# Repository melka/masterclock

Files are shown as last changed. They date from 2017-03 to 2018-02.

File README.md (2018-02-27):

# masterclock

Master clock for Lepaute 30 seconds alternating pulse slave clock and possibly other models.

## background

Slave clocks are old school clocks mostly used in train stations, hospitals, factories, etc... places that needed to have accurate timekeeping and synchronized clocks in a lot of places. A master clock was responsible for keeping time and controlling all the slave clocks. There were a number of clock manufacturers, and there were a lot of way of synching the slave clocks to the master clock.

If you find a beautiful industrial slave clock, there are several options :
* Find the master clock to go with it, but you'll need space, money and time to take care of it
* Remove the old mechanical movement and replace it with a quartz one (shame on you)
* Buy one of [these](http://www.bmumford.com/clocks/driver/driver.html), but what's the fun in that ?
* Make a teeny-tiny master clock.

So here comes this project.

## goal

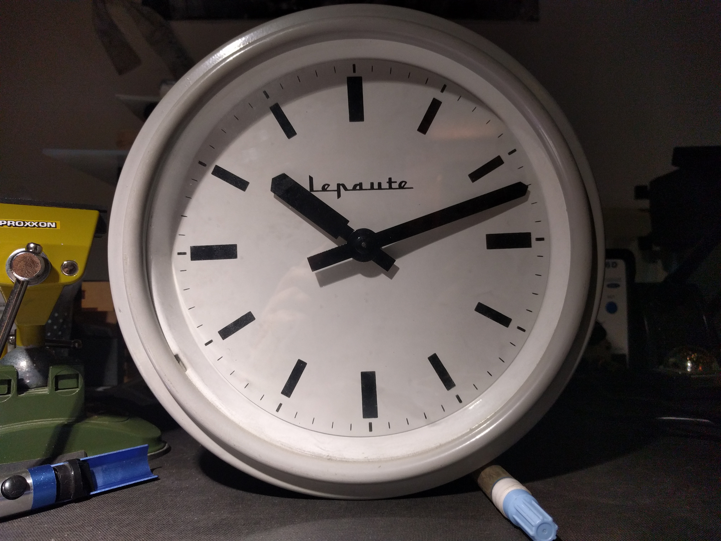
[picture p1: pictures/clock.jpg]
clock


I got hold of two slave clocks that were salvaged from an hospital that was being destroyed in France. One of them is a Lepaute clock.

Those clocks use an alternating pulse every 30 seconds to make the minute hand advance half a minute. The pulse is ~200ms and a 1.5V battery is enough to make it go.

I wanted to make a board that could run for more than a year on a single AA battery, be highly accurate and that would be as small as possible (in this case, just enough space to fit the battery and a screw terminal to plug the clock mechanism).

That was a fail, but mostly due to firmware mistakes. Old one had flaws and kept the clock running approximately 3 1/2 weeks before draining the battery. This new version of the firmware should improve the run time dramatically. New version with new battery installed on February 27 2018 at 8:30PM, let's see how long it'll run...

When all the chips are sleeping, my multimeter shows nothing, and the wake-up time is so short that I can't measure it precisely. I've gotten a [uCurrent Gold](https://www.eevblog.com/projects/ucurrent/), so I can measure some current consumptions, but I'm running into problems getting it to work with my oscilloscope. I'll update with curves and graphes when possible.

## BOM

Full BOM can be found on [mouser](https://www.mouser.fr/ProjectManager/ProjectDetail.aspx?AccessID=3831f781b1)

* [TPS60313](http://www.ti.com/product/TPS60313) : Charge Pump
* [MSP430G2553](http://www.ti.com/product/MSP430G2553) : MCU
* [DS3231SN](https://www.maximintegrated.com/en/products/digital/real-time-clocks/DS3231.html) : I2C RTC
* [DRV8838](http://www.ti.com/product/DRV8838) : Brushed DC Motor Driver

## circuit

Power is provided by a single AA battery.

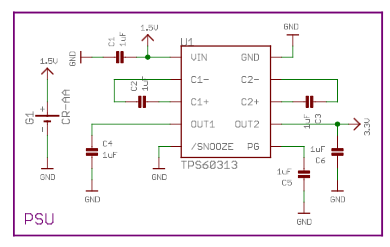
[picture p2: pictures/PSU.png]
PSU


A TPS60313 converts this voltage to 3V in order to power the MCU and RTC. Input voltage can go as low as 0.9V in order to get 3V output. Quiescent current at no-load is 35uA.

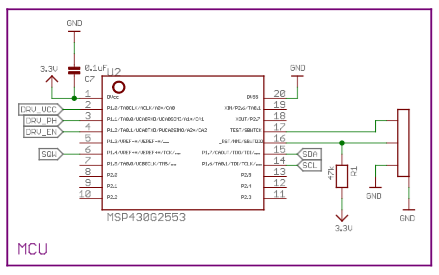
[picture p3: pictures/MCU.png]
MCU


MCU is an MSP430G2553 spending most of its time in LPM4 (consumption should be about 0.15uA). uCurrent shows around 0.105uA.

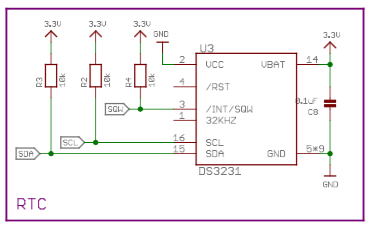
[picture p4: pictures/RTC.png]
RTC


RTC is a DS3231SN, powered only via VBAT to reduce the current consumption of the device. According to the datasheet, Ibatt goes up to 70uA when active, while Ivcc goes up to 200uA. Ibatt when only timekeeping is 0.84uA typical. Measuring with a uCurrent gold shows this number to be accurate.
A DS3231M could be used, but the SN is a tad bit more accurate (+/-2PPM against +/-5PPM for the M).

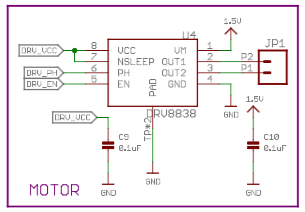
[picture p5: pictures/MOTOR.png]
MOTOR


To drive the mechanism, an alternating pulse is necessary. This could be done with a discrete H-bridge, but I opted for a DRV8838, directly powered from an MCU pin. This way, the DRV isn't even sleeping, but only switched on when needed, once every 30 seconds. Vmotor comes directly from the AA battery.

## on soldering

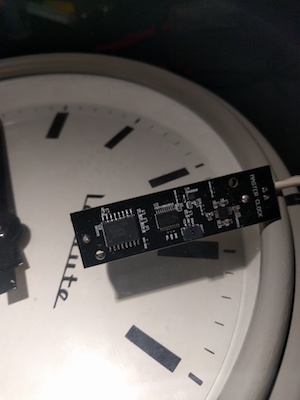
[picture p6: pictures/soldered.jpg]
board


This board being an exercise in miniaturisation, all the resistors and caps are 0402... I advise you not to try to solder this board without a good-ish soldering iron and an hot air gun. I'm using one of the cheap chinese all-in-one stations, but without hot air, some components are next to impossible, especially the DRV8838.

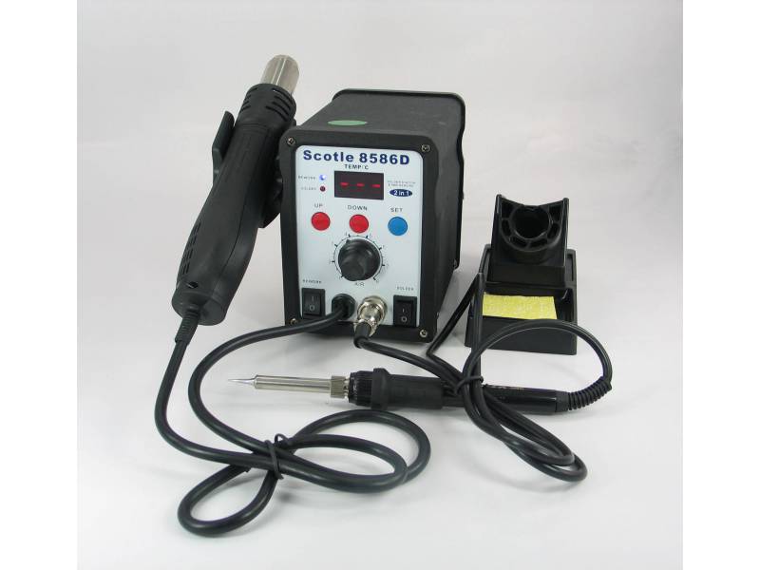
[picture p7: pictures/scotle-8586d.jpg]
soldering


## firmware

Firmware was developed using TI's Cloud IDE since I'm using a Mac and it was the simplest solution.

New version of the firmware configures the RTC to ring 2 alarms : one every time the time goes past HH:MM:00s, the other every time the time goes past HH:MM:30s. The RTC will pull low the interrupt pin 8ms every 30 seconds. Power consumption when the pin is high is microscopic, but it goes up when pulled low. The old firmware was generating a 1Hz square wave with a 50% duty cycle, so the higher current consumption was happening 50% of the time. Now, it should happen only 16ms / minute or 0.00027% of the time...

Old version for information purpose :

```
On boot, the MSP430 runs at 1MHZ and sets some configuration on the RTC :
 * Enable Oscillator
 * Battery-Backed Square-Wave Enable allows the interrupt to be sent when powered by VBAT
 * Rate Select set to 1Hz
 * Interrupt Control set to Square-Wave
 * Disable Alarms
```

P1.4 of the MSP430 is set as an interrupt pin, and then it is put to sleep with external interrupts enabled (LPM4 + GIE).

Every 30 seconds, the RTC pulls P1.4 low, which wakes up the MSP430. We start by clearing the alarm flags of the RTC. A var to keep the inversion of the phase pin is used to check if we should pull P1.1 high or low and inverted each time. We can then proceed to send the enable signal to the DRV8838 so that we advance the needle one step.

MSP430 current consumption while in LPM4 is around 105nA, and 370uA when awaken. The old firmware was waking it up every second for a couple cycles, and then for a full 200ms while sending the pulse every second. Now, we only wake up the MSP430 every 30 seconds for the full 200ms. The old firmware was also toggling the state of P1.1 every 30 seconds, so it was staying high for a full 30 seconds before being toggled low. Now, it's only pulled high if necessary.

Old version for information purpose :

```
Each second, the RTC sends a pulse on P1.4, which wakes up the MSP430. A counter is incremented and when this seconds counter == 30, power is applied to the DRV8838 by putting P1.0 high (DRV_VCC), pulse direction is reversed by toggling P1.1 (DRV_PH) and a 200ms pulse is sent via P1.2 (DRV_EN). Counter is reset and the MSP430 goes back to sleep.
```

### references
 * [Horloge Mère (in French)](http://f5mna.free.fr/h_mere.htm)
 * [Powering an MSP430 From a Single Battery Cell](http://www.ti.com/lit/an/slaa398/slaa398.pdf)

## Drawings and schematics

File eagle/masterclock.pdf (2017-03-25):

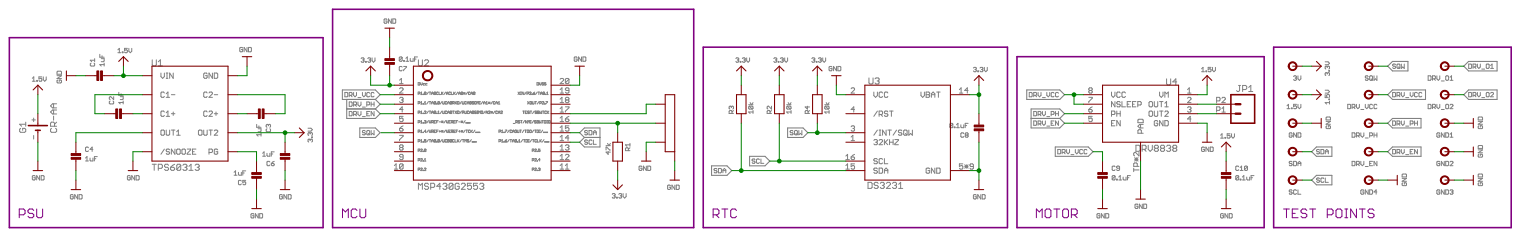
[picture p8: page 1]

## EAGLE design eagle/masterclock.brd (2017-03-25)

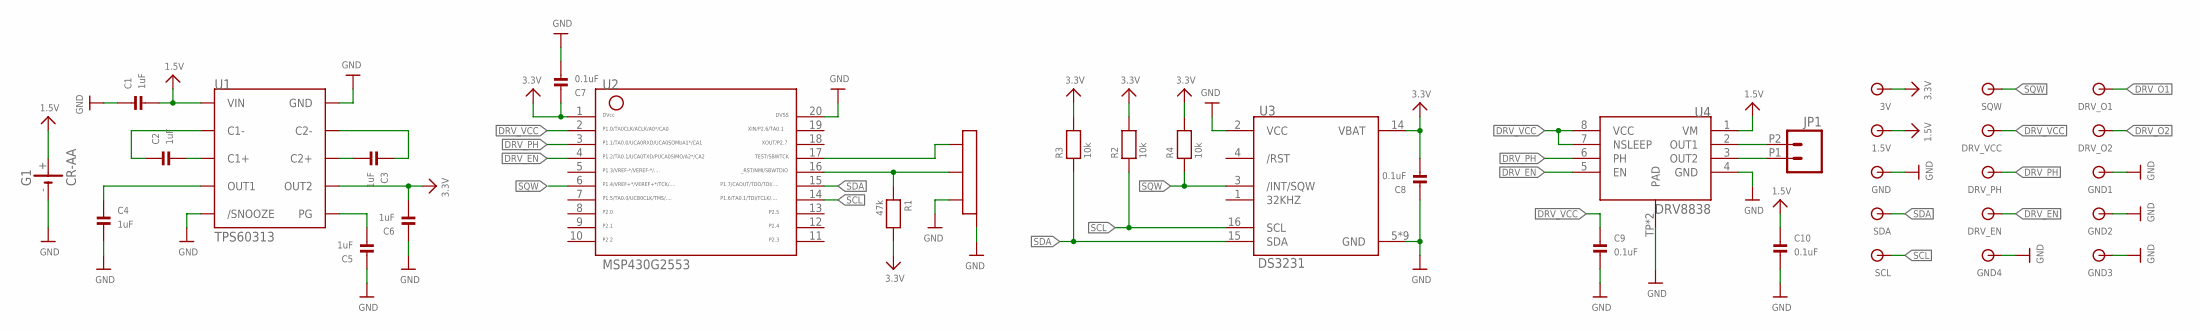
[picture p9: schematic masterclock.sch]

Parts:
1.5V, 3V: TESTPAD
C1, C2, C3, C4, C5, C6: 1uF; 0402
C7, C8, C9, C10: 0.1uF; 0402
DRV_EN: TESTPAD
DRV_O1, DRV_O2: TESTPAD
DRV_PH: TESTPAD
DRV_VCC: TESTPAD
G1: CR-AA; CRAA
GND: TESTPAD
GND1, GND2, GND3, GND4: GND; TESTPAD
JP1: M022.54MM_SCREWTERM; 1X02_2.54_SCREWTERM
R1: 47k; 0402
R2, R3, R4: 10k; 0402
SCL: TESTPAD
SDA: TESTPAD
SQW: TESTPAD
U1: TPS60313; MSOP10
U2: MSP430G2553; PW20
U3: DS3231; SO16
U4: DRV8838; WSON8
U$27: M03; TE-MICRO-MNL-

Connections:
1.5V: 1.5V.P$1, C1.2, C10.1, G1.+, U1.P$3 (VIN), U4.1 (VM)
3.3V: 3V.P$1, C6.2, C7.1, C8.2, R1.2, R2.2, R3.2, R4.2, U1.P$6 (OUT2), U2.1, U3.14 (VBAT)
/RST: R1.1, U2.16, U$27.P$2
DRV_EN: DRV_EN.P$1, U2.4, U4.5 (EN)
DRV_O1: DRV_O1.P$1, JP1.P2 (2), U4.2 (OUT1)
DRV_O2: DRV_O2.P$1, JP1.P1 (1), U4.3 (OUT2)
DRV_PH: DRV_PH.P$1, U2.3, U4.6 (PH)
DRV_VCC: C9.1, DRV_VCC.P$1, U2.2, U4.7 (NSLEEP), U4.8 (VCC)
GND: C1.1, C4.2, C5.1, C6.1, C7.2, C8.1, C9.2, C10.2, G1.-, GND.P$1, GND1.P$1, GND2.P$1, GND3.P$1, GND4.P$1, U1.P$1 (/SNOOZE), U1.P$9 (GND), U2.20, U3.2 (VCC), U3.5 (GND), U3.6 (GND), U3.7 (GND), U3.8 (GND), U3.9 (GND), U3.10 (GND), U3.11 (GND), U3.12 (GND), U3.13 (GND), U4.4 (GND), U4.TP (PAD), U4.TP1 (PAD), U$27.H1, U$27.H2, U$27.P$3
unnamed: C2.2, U1.P$4 (C1+)
unnamed: C2.1, U1.P$2 (C1-)
unnamed: C3.1, U1.P$8 (C2-)
unnamed: C3.2, U1.P$7 (C2+)
unnamed: C5.2, U1.P$10 (PG)
PWROUT: C4.1, U1.P$5 (OUT1)
SCL: R2.1, SCL.P$1, U2.14, U3.16 (SCL)
SDA: R3.1, SDA.P$1, U2.15, U3.15 (SDA)
SQW: R4.1, SQW.P$1, U2.6, U3.3 (/INT/SQW)
TEST: U2.17, U$27.P$1

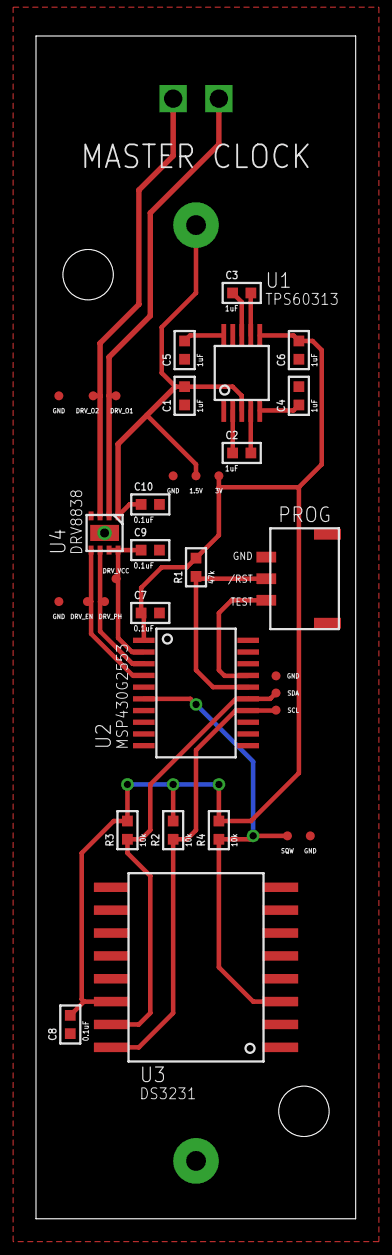
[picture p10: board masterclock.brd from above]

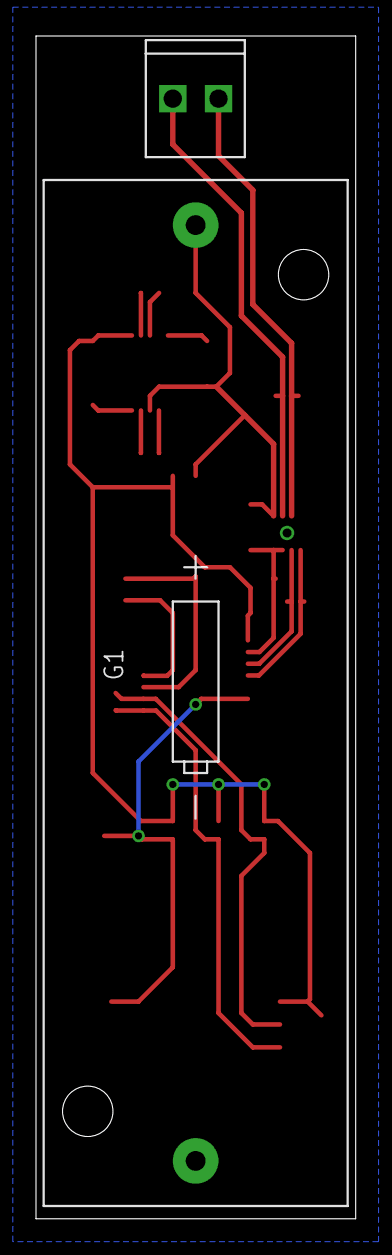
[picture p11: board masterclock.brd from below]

Board: 2 copper layers, 17.8 x 65.7 mm, 36 parts (2 on the bottom side), 19 nets.

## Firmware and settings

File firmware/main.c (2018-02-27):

/* MASTERCLOCK
 * Master clock for Lepaute 30 seconds alternating pulse slave clock and possibly other models.
 * Goal is minimal power consumption on a single 1.5V (AA) battery.
 */

#include <msp430g2553.h>
#include "DS3231.h"
#include "TI_USCI_I2C_master.h"

int invert_phase = 0;

int main(void) {
  // Stop watchdog timer
  WDTCTL = WDTPW | WDTHOLD;

  // Set DCO
  BCSCTL1 = CALBC1_1MHZ;
  DCOCTL = CALDCO_1MHZ;

  P1DIR = 0xFF; // All P1.x outputs
  P2DIR = 0xFF; // All P2.x outputs
  P3DIR = 0xFF; // All P3.x outputs
  // ~360uA
  P1OUT = 0xFF; // All Off
  P2OUT = 0xFF; // All Off
  P3OUT = 0xFF; // All Off
  // ~340uA

  // Set P1.0 at 0 > turn off power to DRV8838
  P1OUT &= ~BIT0;

  // RTC Alarm Interrupt
  P1DIR &= ~BIT4; // Set P1.4 to input
  P1REN |= BIT4; // Enable pullup resistor of P1.4 (default: GND)
  P1OUT |= BIT4; // Set pullup resistor to active (+3.3V) mode
  P1IE |= BIT4; // P1.4 interrupt enabled
  P1IFG &= ~BIT4; // P1.4 interrupt flag cleared

  // Set initial time
  // This is not really important, the only parameter
  // interesting to change would be the second, to have
  // the first pulse earlier or later during boot
  unsigned char start_time[7];
  start_time[0] = DEC_to_BCD(25); // Second
  start_time[1] = DEC_to_BCD(59); // Minute
  start_time[2] = DEC_to_BCD(23); // Hour
  start_time[3] = DEC_to_BCD(2);  // Day of Week / Week start on Sunday : 1
  start_time[4] = DEC_to_BCD(31); // Day
  start_time[5] = DEC_to_BCD(12); // Month
  start_time[6] = DEC_to_BCD(12); // Year

  DS3231_set_time(start_time);

  // Set RTC Alarms
  // Alarm 1 : We want alarm 1 to generate the interrupt
  // eeach time the time goes past HH:MM:30s
  // This would give is a pulse every minute
  unsigned char alarm1_conf[4] = {
      0b00110000,    // A1M1 0 : 30s
      0b10000000,    // A1M2 1 : 0m
      0b10000000,    // A1M3 1 : 0h
      0b10000000     // A1M4 1 : 0d
  };
  // Alarm 2 : Alarm 2 will generate the interrupt
  // every time the time goes past HH:MM:00s
  // This will give us a pulse every minute
  unsigned char alarm2_conf[3] = {
      0b10000000,    // A2M1 1 : 0m
      0b10000000,    // A2M2 1 : 0h
      0b10000000     // A2M3 1 : 0d seconds
  };
  // Alarm 1 + Alarm 2 totals a pulse every 30 seconds

  DS3231_set_alarms(alarm1_conf, alarm2_conf);

  // Set RTC configuration
  // Enable Alarm 1 & 2 on /SQW/INT pin
  unsigned char rtc_conf = 0b00000111;
  DS3231_set_RTCconf(&rtc_conf);

  // Clear alarm flags
  DS3231_clear_alarm_FG();

  // Let's get some zzzz
  __bis_SR_register(LPM4_bits+GIE);
  // 105nA on Sleep, 370uA on wake for MSP430
  // 915nA DS3231 + MSP430 on
}

#pragma vector=PORT1_VECTOR
__interrupt void PORT_1(void) {
    // Go back to sleep when interrupt routine ends
    __bis_SR_register_on_exit(LPM4_bits+GIE);
    // P1.4 interrupt flag cleared
    P1IFG &= ~BIT4;
    // Clear alarm flags
    DS3231_clear_alarm_FG();

    // Power up DRV8838
    // Toggle P1.0 high
    P1OUT |= BIT0;

    // Check if we need to pull P1.1 high
    // to invert the phase of the pulse
    invert_phase = invert_phase == 0 ? 1 : 0;
    if (invert_phase == 1) {
      P1OUT |= BIT1;
    }

    // Enable DRV8838 pulse for 200ms
    P1OUT |= BIT2;
    __delay_cycles(200000);
    P1OUT &= ~BIT2;

    // Pull phase down
    P1OUT &= ~BIT1;

    // Shut down DRV8838
    P1OUT &= ~BIT0;
}

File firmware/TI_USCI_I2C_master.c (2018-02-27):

//******************************************************************************
//   MSP430 USCI I2C Transmitter and Receiver
//
//  Description: This code configures the MSP430's USCI module as
//  I2C master capable of transmitting and receiving bytes.
//
//  ***THIS IS THE MASTER CODE***
//
//                    Master
//                 MSP430F2619
//             -----------------
//         /|\|              XIN|-
//          | |                 |
//          --|RST          XOUT|-
//            |                 |
//            |                 |
//            |                 |
//            |         SDA/P3.1|------->
//            |         SCL/P3.2|------->
//
// Note: External pull-ups are needed for SDA & SCL
//
// Uli Kretzschmar
// Texas Instruments Deutschland GmbH
// November 2007
// Built with IAR Embedded Workbench Version: 3.42A
//******************************************************************************
// Modified for MSP430G2553
// HouYu Li <karajan_ii@hotmail.com>
// April 2013
//******************************************************************************

#include "msp430g2553.h"                        // device specific header
//#include "msp430x22x4.h"
//#include "msp430x23x0.h"
//#include "msp430xG46x.h"
// ...                                         // more devices are possible

#include "TI_USCI_I2C_master.h"

signed char byteCtr;
unsigned char *TI_receive_field;
unsigned char *TI_transmit_field;

//------------------------------------------------------------------------------
// void TI_USCI_I2C_receiveinit(unsigned char slave_address,
//                              unsigned char prescale)
//
// This function initializes the USCI module for master-receive operation.
//
// IN:   unsigned char slave_address   =>  Slave Address
//       unsigned char prescale        =>  SCL clock adjustment
//-----------------------------------------------------------------------------
void TI_USCI_I2C_receiveinit(unsigned char slave_address,
                             unsigned char prescale){
	I2C_PSEL = I2C_SDA + I2C_SCL;
	I2C_PSEL2 = I2C_SDA + I2C_SCL;
	UCB0CTL1 = UCSWRST;                        // Enable SW reset
	UCB0CTL0 = UCMST + UCMODE_3 + UCSYNC;       // I2C Master, synchronous mode
	UCB0CTL1 = UCSSEL_2 + UCSWRST;              // Use SMCLK, keep SW reset
	UCB0BR0 = prescale;                         // set prescaler
	UCB0BR1 = 0;
	UCB0I2CSA = slave_address;                  // set slave address
	UCB0CTL1 &= ~UCSWRST;                       // Clear SW reset, resume operation
	UCB0I2CIE = UCNACKIE;
	IE2 = UCB0RXIE;                            // Enable RX interrupt
}

//------------------------------------------------------------------------------
// void TI_USCI_I2C_transmitinit(unsigned char slave_address,
//                               unsigned char prescale)
//
// This function initializes the USCI module for master-transmit operation.
//
// IN:   unsigned char slave_address   =>  Slave Address
//       unsigned char prescale        =>  SCL clock adjustment
//------------------------------------------------------------------------------
void TI_USCI_I2C_transmitinit(unsigned char slave_address,
                          unsigned char prescale){
	I2C_PSEL = I2C_SDA + I2C_SCL;
	I2C_PSEL2 = I2C_SDA + I2C_SCL;
	UCB0CTL1 = UCSWRST;                        // Enable SW reset
	UCB0CTL0 = UCMST + UCMODE_3 + UCSYNC;       // I2C Master, synchronous mode
	UCB0CTL1 = UCSSEL_2 + UCSWRST;              // Use SMCLK, keep SW reset
	UCB0BR0 = prescale;                         // set prescaler
	UCB0BR1 = 0;
	UCB0I2CSA = slave_address;                  // Set slave address
	UCB0CTL1 &= ~UCSWRST;                       // Clear SW reset, resume operation
	UCB0I2CIE = UCNACKIE;
	IE2 = UCB0TXIE;                            // Enable TX ready interrupt
}

//------------------------------------------------------------------------------
// void TI_USCI_I2C_receive(unsigned char byteCount, unsigned char *field)
//
// This function is used to start an I2C commuincation in master-receiver mode.
//
// IN:   unsigned char byteCount  =>  number of bytes that should be read
//       unsigned char *field     =>  array variable used to store received data
//------------------------------------------------------------------------------
void TI_USCI_I2C_receive(unsigned char byteCount, unsigned char *field){
  TI_receive_field = field;
  if ( byteCount == 1 ){
    byteCtr = 0 ;
    __disable_interrupt();
    UCB0CTL1 |= UCTXSTT;                      // I2C start condition
    while (UCB0CTL1 & UCTXSTT);               // Start condition sent?
    UCB0CTL1 |= UCTXSTP;                      // I2C stop condition
    __enable_interrupt();
  } else if ( byteCount > 1 ) {
    byteCtr = byteCount - 2 ;
    UCB0CTL1 |= UCTXSTT;                      // I2C start condition
  } else
    while (1);                                // illegal parameter
}

//------------------------------------------------------------------------------
// void TI_USCI_I2C_transmit(unsigned char byteCount, unsigned char *field)
//
// This function is used to start an I2C commuincation in master-transmit mode.
//
// IN:   unsigned char byteCount  =>  number of bytes that should be transmitted
//       unsigned char *field     =>  array variable. Its content will be sent.
//------------------------------------------------------------------------------
void TI_USCI_I2C_transmit(unsigned char byteCount, unsigned char *field){
  TI_transmit_field = field;
  byteCtr = byteCount;
  UCB0CTL1 |= UCTR + UCTXSTT;                 // I2C TX, start condition
}
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
